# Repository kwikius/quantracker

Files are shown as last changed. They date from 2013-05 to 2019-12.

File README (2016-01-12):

DIY Antenna Tracker and OSD using STM32F4 .

Ground side tracker.
   Uses a Pololu style servo motor with encoder to give continuous Azimuth rotation
   Uses a standard RC Servo for elevation.
Airborne side 
   uses an OSD with telemetry via the video to send telemetry data to the tracker.
   or an Arduino ( basic option if you have a FrSky Telemetry RC system)

see my website http://www.zoomworks.org/fpv/quantracker/doc/index.html for more info about the project.

See the Changelog file in this directory for changes after 16/07/2013

Acknowledgments

      With Grateful Acknowledgements to the prior work, on the OSD code of:

        Sami Korhonen(Openpilot.org)
        taulabs ( taulabs.com) 
        brainFPV ( brainfpv.com)
        Thomas Oldbury (super-osd.com)
   
        Thanks to VEX Robotics for permission to use their step file of the VEX turntable

        Special Thanks to Andrew Fernie for his work on the Hardware and Software.

Dependencies

   The GNU gcc compiler. The source code is written in C++11, and requires gcc4.7 or higher
   to compile.
   available from 

         https://launchpad.net/gcc-arm-embedded
         (wget https://launchpad.net/gcc-arm-embedded/4.9/4.9-2014-q4-major/+download/gcc-arm-none-eabi-4_9-2014q4-20141203-linux.tar.bz2 -O gcc-arm)

   The STM32F4 standard peripherals library
   available from

         http://www.st.com/st-web-ui/static/active/en/st_prod_software_internet/resource/technical/software/firmware/stm32f4_dsp_stdperiph_lib.zip
         (wget http://www.st.com/st-web-ui/static/active/en/st_prod_software_internet/resource/technical/software/firmware/stm32f4_dsp_stdperiph_lib.zip -O stm32f4_dsp_stdperiph_lib.zip)

   My quan library 
   available from
         
         https://github.com/kwikius/quan-trunk
         (wget https://github.com/kwikius/quantracker/archive/master.zip -O quantracker.zip)

   FreeRTOS
   available from

         http://www.freertos.org/a00104.html
         (wget http://downloads.sourceforge.net/project/freertos/FreeRTOS/V8.2.0/FreeRTOSV8.2.0.zip -O freertos.zip)

   MAVlink
   available from
 
        https://github.com/mavlink/mavlink
        (wget https://github.com/mavlink/c_library/archive/master.zip -O mavlink.zip)
         TODO May need some file dir renaming to get the directories right for compiling

Once these are installed you will need to modify the paths in the Makefiles to suit your configuration.
See the file Sample-Dependencies.mk in the root directory for details of how to fill in dependencies

The ground tracker relies on some means on the aircraft to get the telemetry back to the tracker

The OSD can however be built as stand alone item. There are currenetly 2 customised example OSD,s in the quantracker/examples directory.
airborne option to send the data to the tracker from the aircraft.

So far there are several airborne options

  1) Use the OSD airborne module which uses the Video link direct to send telemetry.
     This is currently in development but the design is all open source and in the repo.
     I hope to have a retail version soon.

  2) using an Arduino Pro Mini microcontroller and an FrSky Rx ( simple cheap)

     a) Use an Frsky Telemetry receiver and an Ardupilot to acquire the GPS data.
      The source code for this option can be downloaded from

         https://github.com/kwikius/mavlink_to_frsky

     b) Use a GPS module attached direct to the Arduino and sending data down the FrSky telemetry link
      The source code for this option is available at
         
         https://github.com/kwikius/quantracker_air

----

   There are various other applications associated with the project. 

      See https://github.com/kwikius?tab=repositories for more details

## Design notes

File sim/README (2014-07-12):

PC simulator for my Antenna Tracker with a GUI to move the aircraft around
 and send the simulated GPS info to the Tracker.

See http://www.zoomworks.org/fpv/antenna_tracker/index.html for more about info about the Tracker.
See https://github.com/kwikius/mavlink_to_frsky for the airborne part of the project.
See https://github.com/kwikius/quantracker for sourcode for the tracker part of the project

The code is written in C++11 , so you will need gcc4.7 or above to compile and build.

Currently builds for Linux only.

Other dependencies:
 
	wxWidgets http://www.wxwidgets.org/
	my quan library:  https://github.com/kwikius/quan-trunk

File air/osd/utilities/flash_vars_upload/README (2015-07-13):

README for flash_vars.exe

This app can be used to read to :

   *  Write the flash variables to the OSD from a file
   *  Read  the flash variables to a file from the OSD. The file can then be used to
      write the Flash on other boards
   
There should be a sample file called osd_params.txt in this directory.
in the file empty lines and lines starting with '#' should be ignored

sample read invocation:
# ./flash_vars.exe -read osd_params.txt -port /dev/ttyUSB0

sample write invocation:
# ./flash_vars.exe -write osd_params.txt -port /dev/ttyUSB0

Changelog

Can now read from flash variables to a file

Fixed vector values can now contain whitespace
  e.g [ 1 ,2 , 3 ] is accepted

Fixed so that accepts return and linefeed as end of line char
Now automatically exits to start OSD when done. (Hope eventually to do it interactively
, so its wysiwyg)

Issues. 
- Check that the OSD is on and connected in flash menu mode. 
**If it isnt this app doesnt notice** So do look at the output
You can tell if its working by the text or lack of returned by the OSD.

- The array values shouldnt contain spaces else will fail,
 e.g [1,2,3] not [ 1 ,2 , 3 ] (Hope to fix this at some stage)

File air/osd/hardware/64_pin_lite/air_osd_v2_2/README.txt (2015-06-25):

The Quantracker Air OSD V2.2 files in this zip file are also available at https://github.com/kwikius/quantracker/tree/devel/air/osd/hardware/64_pin_lite/air_osd_v2_2/

*components/*
   contains "placement_bom.csv", the component placement BOM and  "component_orientation.txt", a specification of the component orientation . 
   
   	If the component orientation specification and  the resulting placement BOM is unsatisfactory, I will be happy to redo it
   	using an alternative transform for the components if you wish.
   	
      In the placement BOM, I have left the part numbers for the chip resistors and capacitors blank since you may prefer to use your own stock, however 
      I can provide some part numbers if this is more convenient. I can also provide more detailed component information if required.

*pcb/*
   contains The Gerber and Drill files.
   	The Gerber files are available in Gerber, Pdf and Postscript formats in the gerber/ subdirectory
  	   The pdf_gerbers/ and postscript_gerbers/ subdirectories contain mirrored and un-mirrored versions of the bottom layer Gerber files as pdf's and postscript format for viewing.
  	   gerbers-README.xls contains some information to help identify the layers the Gerber files represent and the suggested layup.
   
*schematic/*
   contains the schematics for the project in Pdf and Postscript formats. The kicad_project/osd.sch file can be navigated using KiCAD EESchema if preferred.

*kicad_project/*
   contains KiCad project files and some raw KiCAD output. Please be aware that some of the raw kicad output has been modified to try to fit a more standard format.

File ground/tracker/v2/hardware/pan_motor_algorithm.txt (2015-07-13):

Pan motor servo algorithm

variables
pan_motor{
 target_position;     
 target_velocity;
 desired_velocity_at_target;     
 actual_position;
 actual_velocity ;
 actual_current;
}

Unlike a position servo this one may want to be moving
Lookup target_velocity for position_error and  add desired_motor_velocity_at_target

interrupt on compare
1) calc_pwm_for next_cycle
2) start_pwm
3) end_pwm. start pan_motor_current conv
4) get pan_motor_current. calc time to start v sampling
5) start of vsampling set up DMA or irq to read velocity
6) end of vsampling dma or irq

resources

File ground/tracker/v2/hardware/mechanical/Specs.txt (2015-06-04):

-------------------------
CAD drawing of V2 tracker
-------------------------

Conventions
When horizontal and facing north, tracker looks along increasing x axis
When standing upright facing North, then Increasing Y is West
Increasing Z is up.

Axes.
The Tracker tilts around the Y axis.
The tracker pans around the Z axis.
So the intersction of the pan and tilt axes is at [0,0,0]

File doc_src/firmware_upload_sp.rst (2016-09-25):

`OSD Index`_

======================================
Uploading firmware via the Serial Port
======================================

--------
Hardware
--------

   To flash with stm32Flash you need a PC serial port and a USB TTL serial connector.
   A 6 pin Arduino Serial connector works well. It can be either a 3 volt
   or 5 volt one [1]_, but must have power out, since the programming serial port
   is electrically isolated from the rest of the board. When connected
   a red LED should light right by the connector.
   Make sure that you connect to the OSD board with the Black wire
   connected to the V-Blk pin on the 6 way connector.

   

   Alternatively you can use any usb to TTL serial connector and connect the pins appropriately.
   The OSD pins have some protection so within reason it should be possible to swap the Tx and Rx
   connections if it isnt working. Usually (but not always) TX at one end connects to RX at the other
   and vice versa

----------
Stm32flash
----------

   Whichever operating system you use, you need stm32flash. For windows,
   download and unzip `stm32flash_win.zip`_ .

   For Linux, Download Stm32flash_ and  make [sudo] make install. You may also need to add yourself to the 'dialout'
   group to allow you access to the usb serial port: ``sudo usermod -a -G dialout $USER`` ( You will need to reboot for the change to take effect)

   For a quick and dirty upload with stm3flash, get `your desired firmware`_ and
   move the stm32flash executable into the same directory as the firmware.

   Test the execution by starting a command prompt,
   navigating to the directory where the firmware is and issuing 'stm32flash' (for Linux)
   or 'stm32flash.exe'(for Windows),
   to see if it's installed. It should show a page or so of help info.

----------------------------
Find the correct serial port
----------------------------

.....
Linux
.....

   The easiest way on Linux is to remove any usb peripherals except the usb serial connector
   and type

       ``$ setserial -g /dev/ttyUSB[01234]``

   which responds with

       ``/dev/ttyUSB0, UART: unknown, Port: 0x0000, IRQ: 0, Flags: low_latency``

   when I connect my Serial USB adaptor. To be honest if
   you have no other USB serial connectors plugged connected it will usually be /dev/ttyUSB0

.......
Windows
.......

   In Windows remove any extraneous usb devices except the usb serial connector
   and open Device Manager (type Device Manager in
   the box at the bottom of the start menu and it should come up in the list).
   Look for The Ports(COM & LPT) section and there should be an item saying 'USB Serial Port' (COMx)
   where x is a number e.g (say) COM6

----------------------
Powering The OSD board
----------------------

   You will need a power supply of between 8 and 12 Volts [2]_
   to the board ( A servo connector with power and ground connected to (say) a 12 V (3S) lipo is fine)
   and ideally a switch to be able to switch it on and off, though you can just use the connector
   but a switch makes it much easier.

------------------------------------
Checking the OSD board is recognised
------------------------------------

   When using this method of uploading, it is important to follow the sequence
   exactly as described, including the connection sequence.

   *
      Make sure that *Power is Not Connected*
      ,but that it is easy to connect power without disturbing the board.
      Ideally put a switch in the power lead.
      The reason is that touching the board or jiggling the wires
      when connecting can send spurious signals as wires connect
      and disconnect and result in the bootloader on the board not
      recognising the startup sequence correctly [3]_.

   *	Connect the programming jumper on the osd board.
   *   Connect the serial connector to the board and the PC.
   *
      Verify all connectors are the correct way round.
      The connectors are not polarised, so check and check again.

   *  At a command prompt navigate to the directory with the 'xxxx.bin' binary in.
   *
      -   Linux

         +   Assuming you are on /dev/ttyUSB0  ...
         +   *Without Pressing return after yet*, type the command 'stm32flash /dev/ttyUSB0'.

      -   Windows

         +   Assuming you are on COM6  ...
         +   *Without Pressing return after yet*, type the command 'stm32flash.exe COM6'.

   *  Switch on power to the board *without joggling the wires or touching the board* .
   *  Now Press [return] !
   *
      At this point you should see a diagnostic showing that the connection is good.
      It should look something like this::

            stm32flash - http://stm32flash.googlecode.com/

            Serial Config: 57600 8E1
            Version      : 0x31
            Option 1     : 0x00
            Option 2     : 0x00
            Device ID    : 0x0413 (STM32F4xx)
            RAM          : 128KiB  (8192b reserved by bootloader)
            Flash        : 1024KiB (sector size: 4x16384)
            Option RAM   : 15b
            System RAM   : 29KiB

            Resetting device... done.

      If not:

         + Check you are on the correct serial port using the diagnostics for your system (as stated above).
         + Check you have put on the Programming jumper.
         + Check your connections and check you didnt joggle the board too much when turning on power.

   *
      If everything is ok, then, assuming you are in the directory where your firmware
      '.bin' file is, disconnect power [4]_.

-------------------------
Programming the OSD board
-------------------------

   *  Do the steps as above, but this time change the command( assuming your firmware is called 'my_osd_firmware.bin):

  		-   Linux

  			+  'stm32flash -f -v -w my_osd_firmware.bin /dev/ttyUSB0'

  		-   Windows

  			+  'stm32flash.exe -f -v -w my_osd_firmware.bin COM6'

   *
      At this point you should see the same diagnostic as before.
      Then things will appear to hang for maybe 15 seconds with no more output, so be patient::

            stm32flash -f -v -w main.bin /dev/ttyUSB0
            stm32flash - http://stm32flash.googlecode.com/

            Using Parser : Raw BINARY
            Serial Config: 57600 8E1
            Version      : 0x31
            Option 1     : 0x00
            Option 2     : 0x00
            Device ID    : 0x0413 (STM32F4xx)
            RAM          : 128KiB  (8192b reserved by bootloader)
            Flash        : 1024KiB (sector size: 4x16384)
            Option RAM   : 15b
            System RAM   : 29KiB

   *
      Eventually you should see a progress message that the firmware is being loaded.
      This process can take a while so remember not to jiggle the board meanwhile.

   *
      Finally you should see something like the following::

            Wrote and verified address 0x080271c4 (100.00%) Done.

            Resetting device... done.

   *  Congratulations! .. Your firmware  should now be loaded on the board.

   *
      Final important step before testing its working.
      *Unplug the Programming Jumper* (Its easy to forget that step!).

`OSD Index`_

.. _`your desired firmware` :
   osd/firmwares.html
.. _`stm32flash_win.zip`:
   https://github.com/kwikius/quantracker/blob/master/bin/stm32flash_win.zip?raw=true
.. _Stm32Flash: http://stm32flash.googlecode.com
.. _`OSD Index`: osd/index.html
.. _`click here for the pinout`: v1_board.html

.. [1] You only need to connect the pins in bold in the diagram.
.. [2] It should be ok to power the board from up to 25 volts. It just hasnt been verified yet.
       Use the 12V power supply inputs rather than the 3V or 5V breakouts to power the board
       , since the startup time of the psu gives a smooth wakeup from reset.
.. [3] (This is another issue with V1 board. Ideally this can be done better on V2).
.. [4] Disconnecting power executes a reset.

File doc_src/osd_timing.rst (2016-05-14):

----------
OSD Timing
----------

The OSD uses 4 timers to control the OSD [1]_. See the diagram

  

   * Line counter
        In External synch mode Listens to the csynch pulse and counts lines
        Has 4 compare channels
         - Ch1 starts the telemetry lines
         - Ch2 ends the telemtry lines
         - Ch3 starts the OSD rows
         - Ch4 ends the OSD rows
        In internal synch mode, generates the video timing
   
   * Line timer
        Starts at the beginning of telem and OSD rows.
        Has 2 channels
          - Ch1 Opens the gate for the pixel clock
          - Ch2 closes the gate for the pixe clock
            
   * pixel-clock
         Runs as a slave of the Line timer when the gate is opened

   * Idletime sync sep measurer
         This timer

. [1] It should be possible to reduce this, TODO.

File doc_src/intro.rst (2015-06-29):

`Quantracker Index`_

=============================================== 
Introducing Quantracker Antenna Tracker and OSD
===============================================

   * `The Antenna Tracker`_
         + `More on the Antenna Tracker...`_

   * `The OSD`_
         + `More on the OSD...`_

.. * _`The Antenna Tracker`

.............................
The Antenna Tracker
.............................

   Cost effective
         The price of the Tracker should be under £100 ($150). The price of the original
         was around £120 ($180). The next iteration should save over that.

   Compact and Lightweight.
      The tracker should be small, capable of fitting in a backpack neatly
      and should be quick and easy to set up at the flying site

   Simple and reliable
      The tracker should be simple to build and use and reliable in use.

   Performance
      From the outset, the tracker has been designed with performance in mind.
      The tracker can rotate continuously in Pan, unlike some servo based trackers.

   Open source hardware and software
      `The source code is available from Github`_

   Optional ground side OSD
      As time goes on and with the high bandwidth data from the video telemetry
      It should be possible to identify a point in space through the OSD so allowing
      , for example, the position of other aircraft to be displayed.

   Continuous rotation in Pan
       The tracker uses sliprings allowing continuos rotation in pan

   Various ways to send telemetry including but not limited to
         
         + Via the video feed itself ( like teletext).
         + Via one or both of the video audio channels.
         + Via an FrSky telemetry receiver.
         + A combination of any or all of the above.

.. raw:: html

   <table><tr>
   <td>
   <iframe width="420" height="315" src="https://www.youtube.com/embed/uj_cmHMo7XM" 
   frameborder="0" allowfullscreen></iframe>
   </td>
   <td>
   <iframe width="420" height="315" src="https://www.youtube.com/embed/85SXBYkTdV0" 
   frameborder="0" allowfullscreen></iframe>
   </td>
   </tr></table>

.. `The OSD`_

.......
The OSD
.......

The On Screen Display (OSD) grew out of the inital project. 
It turns out that the video signal is capable of transmitting
and receiving at a good data rate. As the design of the airborne
transmitter continued, it was decided to make the
airborne unit a full OSD, for which the ecosystem is now well underway.

   Features
      * Open source software and hardware 
         +  `The OSD V2.1 PCB is available from OSHPark`_
         +  `The OSD source code is available from Github`_

      * Compact.
      * Freestanding - can be used with or without the tracker.
      * Works with Ardupilot, Compatible with MinimOSD. 
      * supports PAL and NTSC cameras (can switch between protocols dynamically).
      * Vector graphics.
      * Hugely customisable display, using "osd_maker" App for helping to create the display.
      * Digitally isolated Serial port to help eliminate ground loops.
      * Very versatile Expansion port with I2C, SPI etc, means the OSD can be upgraded to a full FC

   Here are some videos of the OSD in action:

.. raw:: html

   <table><tr>
   <td>
   <iframe width="420" height="315" src="https://www.youtube.com/embed/cclQAswRa8s" 
   frameborder="0" allowfullscreen></iframe>
   </td>
   <td>
   <iframe width="420" height="315" src="https://www.youtube.com/embed/Czrd15weBXM" 
   frameborder="0" allowfullscreen></iframe>
   </td>
   </tr></table>

`Quantracker Index`_

.. _`The OSD V2.1 PCB is available from OSHPark`: https://oshpark.com/shared_projects/yiU4RsLa
.. _`The source code is available from Github`: https://github.com/kwikius/quantracker/tree/master
.. _`The OSD source code is available from Github`: https://github.com/kwikius/quantracker/tree/master/air/osd
.. _`Quantracker Index`: index.html
.. _`More on the Antenna Tracker...`: ../../antenna_tracker/index.html
.. _`More on the OSD...` : osd/index.html

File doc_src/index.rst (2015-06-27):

`Home`_

=================
Quantracker Index
=================

-----------------------
Antenna Tracker and OSD
-----------------------

..................
Index of sections
..................

* `Introducing the Antenna Tracker and OSD`_

  + `OSD Index`_

  + `Antenna Tracker Index`_

.. _`Introducing the Antenna Tracker and OSD`: intro.html

.. _`OSD Index`: osd/index.html
.. _`Antenna Tracker Index`: ../../antenna_tracker/index.html
.. _`Home`: ../../../index.html

`Home`_

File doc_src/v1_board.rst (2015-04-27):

Index_

--------------------------------
The Quantracker Air OSD V1 board
--------------------------------

The V1 board is not recommended to use except as a test board. 
We would recommended the V2.1 at the moment.
The V1 board had major issues with jamming GPS. 
Passing a frequency scanner over it there was found to be a large spike
at 1575 MHz which is the GPS frequency,
therefore the V1 board is not considered flyable.
However here, for completeness, is the serial port pinout for connecting MAVLink and uploading firmware

  

and here is the pinout of the board itself 

  

.. _Index: index.html

Index_

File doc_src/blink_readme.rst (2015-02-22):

Index_

Blink
=====

Blink is a basic test firmware for the quantracker air osd V1 pcb. 
which blinks the Red heartbeat LED at around 1 Hz to test that the mcu is up and running.
The firmware file is called blink.bin and is in the quantracker/air/osd/test_firmware/blink/ directory.

See the FirmwareUpload_ section for details of how to upload the blink firmware the board.

Index_

.. _FirmwareUpload: ../../../../firmware_upload.html

.. _Index: ../../../../index.html

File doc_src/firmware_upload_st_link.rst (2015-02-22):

Index_

======================================
Uploading firmware using ST-Link
======================================

  If you have a STM32 Discovery board, an STM32 Nucleo or a STLink programmer, then you can use ST-Link. 
  For this method you will also need to make up a programming cable. 
  Using this method you can also runtime debug the board.
  In Linux, you may need to edit your UdevRules_ so you can access the port. 
  The zip contains the relevant udev files which you can add to /etc/udev/rules.d/
 
  * Windows
      ST-Link for windows can be downloaded and installed from [???] (You can also use TexaneSTLink using MinGW). This is a GUI application, though its also useable from command line
  
  * Linux
  		TexaneSTLink_ 

STLink Hardware
---------------

  To flash with ST-Link, you need the ST-Link software,
  a PC usb port and either a STM32xx-Discovery or a STM32xx-Nucleo. 
  You will also need to make a connector.

  * Windows

   -
      Download the ST-LINK software from http://www.st.com/internet/evalboard/product/251168.jsp
      Somewhere down the pag, Find "Associated software"
      There are links to two zip files. Note that they are a Free Download.
      Download the files and unzip them.
      In each resulting directory there is an installer.
      One is for the ST-LINK utility and the other is for the STLINK USB drivers 
      which Windows needs for the USB programming cable. 
      After running both installers you should have a new icon on the desktop, 
      the STM32 ST-LINK Utility.
   -
      Before continuing, you should now download the firmware from 
   -  make the connector [TODO pic of connector]
   -  Start the ST-LINK Utility Application.
   -  
      Connect to the board using Target>Connect from the Top menu.
      (You may get a warning saying the ST-LINK firmware is outdated. You can ignore this.)
   -
      Open the firmware file using File>Open File from the Top menu ..
      In the first tab above the area showing the device memory make 
      sure that "Device Memory @ 0x8000000:" is selected

   - 
      Now program the device using "Target> Program" Or "Target> Program & Verify" 
      Its easiest to deselect the Reset after programming tickbox 
      ( Not essential but we can do a reset by hand for clarity)

   -
      Select Target> Disconnect and quit the application,
      while leaving the cable and pcb connected.

Index_

.. _Index: index.html
.. _Stm32Flash: http://stm32flash.googlecode.com
.. _TexaneSTLink: https://github.com/texane/stlink/
.. _UdevRules: https://wiki.archlinux.org/index.php/udev

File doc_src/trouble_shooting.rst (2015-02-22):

----------------------------
Testing and trouble shooting
----------------------------

* Blink_

.. _Blink: air/osd/board_test/blink/readme.html

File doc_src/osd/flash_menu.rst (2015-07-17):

`OSD Index`_

------------------------------
Quantracker Air OSD Flash Menu
------------------------------

For the `osd_example1`_ and `osd_ac`_ firmwares, you can access the flash menu as follows. [#no_con_change]_

Connect a usb serial connector to the board. 
(A 3V or 5V Arduino serial connector will work fine)

  

Start a serial port console at 9600 baud with 8 bits, no parity and 1 stop bit.
Note that power must be supplied to the port which is electrically isolated
from the rest of the OSD. You can however use any supply from 3 to 5V . The supply is 
usually present on an FTDI to USB cable. 
When power is supplied a red LED will be lit close by the port.

Next supply power to the OSD. It is easiest if you use a switch inline in the power
supply rather than fumbling with connectors
When you switch on the OSD, The Serial console should present you with something similar to:

::
  
   Press return 3 times for Flash Menu

Then after a few seconds

::

   Time is up! ... Exiting to Flight mode

However if you press return 3 times immediately ( up to 3 seconds) after startup you should be
presented with:

::

   Quantracker Air OSD 2.1
   ~~~~Flash menu mode~~~~

You are now in Flash menu mode.

The various functions are available as commands.

   * help
      Displays a list of the available commands with options

   * info
      Displays some useful info. For info about a particular variable type the name
      of the variable after the command

   * show
      Displays the current values of the variables.
      For value of a particular variable type the name
      of the variable after the command. Varaiables not yet defined are shown as '#undef#'
      In case of undefined variables default values are used in the osd.

   * set
      Set variable to value. Requires the name of the variable and a value in correct format.

   * exit
      Exit the flash menu mode and start showing the OSD.

To set the values of flash variables all at once go you can also use the app in 
      `quantracker/air/osd/utilities/flash_vars_upload/`_ . See the readme there for details.

.. _`quantracker/air/osd/utilities/flash_vars_upload/`: 
   https://github.com/kwikius/quantracker/tree/master/air/osd/utilities/flash_vars_upload
.. _`OSD Index`: index.html
.. _`osd_example1` : firmwares/osd_example1.html
.. _`osd_ac` : firmwares/osd_example1.html

.. [#no_con_change]  This has been changed from earlier versions so that there is no need to change connectors to enter 
         flash menu mode

`OSD Index`_

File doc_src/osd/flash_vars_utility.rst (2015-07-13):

--------------
Flash_vars.exe
--------------

This app can be used to read to :

*  Write the flash variables to the OSD from a file
*  Read  the flash variables to a file from the OSD. 

A file read from a board can then be used to write the Flash on other boards.
   
There should be a sample file called osd_params.txt in this directory.
in the file empty lines and lines starting with '#' should be ignored

Usage:
   Connect the OSD to the PC via usb cable, but dont switch on the OSD
   run flash_vars.exe on the PC
   You should see a message to say
   
::

   -----------------Ready to Upload-------------------------
   Switch on the OSD board and then immediately press any key

On switching on the OSD it will wait approx 3 seconds looking for the sequence to
start the flash menu so if the flash_vars is too late it will not catch it.

If all goes well however, The Flash Variables file will be uploaded or downloaded to/from the OSD.

sample read invocation:

::

   ./flash_vars.exe -read osd_params.txt -port /dev/ttyUSB0

sample write invocation:

:: 

   ./flash_vars.exe -write osd_params.txt -port /dev/ttyUSB0

Changelog

* Can now read from flash variables to a file

* Fixed vector values can now contain whitespace
  e.g [ 1 ,2 , 3 ] is accepted

* Fixed so that accepts return and linefeed as end of line char
  Now automatically exits to start OSD when done. (Hope eventually to do it interactively
  , so its wysiwyg)

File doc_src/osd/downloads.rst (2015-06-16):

----------------------
OSD firmware downloads
----------------------

Since the board is a Dev board we are currently providing  some example firmwraes that are designed to be customised.
As the OSD develops we hope to  develop some classic themes. Below are the firmwares that we have currently. 

........
Example1 
........

Download from Github `firmware_example1.bin`_

This OSD firmware is designed as a minimal but useful display for use with fixed wing aircraft.

The display widgets consist of
 - a compass with integral home arrow, 
 - an artificial horizon 
 - battery voltage
 
 When the OSD display starts up and while it is waiting for a GPS lock, it displays the number of satellites and the gps status.
 
 Once a valid satellite fix is obtained, the OSD assumes it is at the home position and the Display stops showing satelliete status 
 and shows the altitude and distance from home. 

.. _`firmware_example1.bin`: https://github.com/kwikius/quantracker/blob/master/examples/osd_example1/board/main.bin

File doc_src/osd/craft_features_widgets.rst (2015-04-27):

`OSD Index`_

=========================================
craft, features and widgets.
=========================================

This section deals with my ramblings on how to categorise the things you might put on the OSD. 
The current solution is to split the OSD into ones own personal project,
however there should be eventually be a library or libraries of common stuff. 

   Craft
         Could be one of:

            + aircraft
            + watercraft
            + land vehicle
            + amphibious vehicle
            + submarine
            + etc

   Features
         Variables representing fine grained aspects of the crafts behaviour/properties/state.
         Some examples of Features of a craft. A craft may or may not have 
         a particular feature [#craft_feature]_ .

            + current time
            + current latitude
            + current longtitude
            + current altitude 
            + current pitch
            + current yaw
            + current roll
            + batteries
               - so ... Number of batteries, name per battery, capacity per battery, voltage etc?

   Widgets
         Widgets are designed based on the features they require to work [#widget_robust]_ .

            * MyCompassWidget    - requires feature current yaw 
            * MyHomeArrowWidget - requires features current latitude,current Longitude
            * MyAltitudeWidget   - requires feature Altitude ( yes really :) )
            * MyArtificialHorizonWidget - requires current pitch and current roll.

   global-feature-list
         A global list of features available, with comprehensive definitions
 
   user-feature-list 
         The features of the users craft, selected from the global list of
         features.

   available-widget-list
         A set of widgets that are available for use.
         May comprise Widgets that have been accumulated from various sources
         or created by the user or both.

   user-widget-list 
         The available-widget-list is filtered by the user-feature-list to select
         only those that use features on the user-feature-list [#filter_override]_ :

   user-firmware
         The user firmware is generated from the user-widget-list. 

`OSD Index`_

.. _Features: http://www.wikipedia.org/wiki/Feature_(machine_learning)
.. _`OSD Index`: index.html

.. [#craft_feature]  A craft with a GPS can be assumed to have latitude, longtitude, altitude etc.
.. [#widget_robust]  Widgets must be designed to be able to cope with failed requests for data.
.. [#filter_override]  It should be possible to override the filter, so a user can test some feature.

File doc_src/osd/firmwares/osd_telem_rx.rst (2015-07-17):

`OSD Index`_

---------------------
osd_telem_rx firmware
---------------------

osd_telem_rx:
   This OSD firmware is designed to demonstrate the use of the video signal to transmit data.
   You will need 2 boards. The second board should run the `osd_telem_tx firmware`_. For testing
   you can connect the transmitter OSD board video out to the receiver OSD board video in.
   The display simply shows a timer. You can customise what is shown on the osd
   See the on_telemetry_received() function defined in 
   `quantracker/examples/osd_telem_rx/rx_telemetry.cpp`_ for details.
   There is `more technical info about the telemetry here`_

   `Download osd_telem_rx firmware`_

.. _`Download osd_telem_rx firmware`: 
   https://github.com/kwikius/quantracker/blob/master/examples/osd_telem_rx/bin/main.bin?raw=true
.. _`OSD Index`: ../index.html
.. _`osd_telem_tx firmware`: osd_telem_tx.html
.. _`more technical info about the telemetry here`: ../software_devel/tech/telemetry.html
.. _`quantracker/examples/osd_telem_rx/rx_telemetry.cpp`:
   https://github.com/kwikius/quantracker/blob/master/examples/osd_telem_rx/rx_telemetry.cpp

`OSD Index`_

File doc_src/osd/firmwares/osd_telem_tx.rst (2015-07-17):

`OSD Index`_

---------------------
osd_telem_tx firmware
---------------------

osd_telem_tx:
   This OSD firmware is designed to demonstrate the use of the video signal to transmit data.
   You will need 2 OSD boards. The second OSD board should run the `osd_telem_rx firmware`_ . For testing
   you can connect the transmitter board video out to the receiver board video in.
   The display simply shows a timer. 

   You can customise what is sent. 
   See the ``on_telemetry_transmitted()`` function defined in 
   `quantracker/examples/osd_telem_tx/tx_telemetry.cpp`_ for details.
   `More technical info about the telemetry here`_

   `Download osd_telem_tx firmware`_

.. _`Download osd_telem_tx firmware`: 
   https://github.com/kwikius/quantracker/blob/master/examples/osd_telem_tx/bin/main.bin?raw=true
.. _`OSD Index`: ../index.html
.. _`osd_telem_rx firmware`: osd_telem_rx.html
.. _`More technical info about the telemetry here`: ../software_devel/tech/telemetry.html
.. _`quantracker/examples/osd_telem_tx/tx_telemetry.cpp`:
   https://github.com/kwikius/quantracker/blob/master/examples/osd_telem_tx/tx_telemetry.cpp

`OSD Index`_

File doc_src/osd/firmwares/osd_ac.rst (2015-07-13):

`OSD Index`_

---------------
osd_ac firmware
---------------

   This firmware provides:

   * 4 configurable pages switchable from an RC channel
   * Many Mavlink variables that can be switched in or out per page

   `Download osd_ac firmware`_

.. raw:: html

   <iframe width="420" height="315" src="https://www.youtube.com/embed/Czrd15weBXM" 
   frameborder="0" allowfullscreen></iframe>

.. _`Download osd_ac firmware`: https://github.com/kwikius/quantracker/blob/master/examples/osd_ac/board/bin/main.bin?raw=true
.. _`OSD Index`: ../index.html

`OSD Index`_

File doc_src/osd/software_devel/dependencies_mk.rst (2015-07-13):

`OSD Index`_

------------------------
The Dependencies.mk file
------------------------

Dependencies.mk is a makefile in the quantracker root directory
whose sole purpose is to let the quantracker makefiles 
know where to find the quantracker `dependent libraries`_ ( in other words the software 
libraries that quantracker depends on to build) see `toolchain.html`_ for details
about where to get these libraries. [#installer]_ 
You can also save the template root directory file "Sample-Dependencies.mk" 
as Dependencies.mk and edit the contents.

The format to define a makefile-variable is simply

VARIABLE = expression

(`See here more info on GNU Make`_ )

The following variables need to be defined. [#trailing]_ 

TOOLCHAIN_PREFIX 
   The top-level directory to the arm-gcc compiler toolchain. e.g if your toolchain is in
   /home/kat/armgccv1 it would  be defined as TOOLCHAIN_PREFIX= /home/kat/armgccv1/

TOOLCHAIN_GCC_VERSION 
  The version of arm-gcc. The gcc version must be equal to or greater than 4.7, as the quantracker library
  makes much use of C++11 features. You can find your arm-gcc version by
  navigating at the command line to the top-level directory of the arm-gcc toolchain. 
  From there go to the bin subdirectory and invoke  './arm-none-eabi-gcc --version'
  The output should be something like :
   
  :: 

     arm-none-eabi-gcc (GNU Tools for ARM Embedded Processors) 4.9.3 20141119 (release) [ARM/embedded-4_9-branch revision 218278]
     Copyright (C) 2014 Free Software Foundation, Inc.
     This is free software; see the source for copying conditions.  There is NO
     warranty; not even for MERCHANTABILITY or FITNESS FOR A PARTICULAR PURPOSE.

  In the above case the version is 4.9.3

STM32_STD_PERIPH_LIB_DIR 
   The path to the STM32 std peripherals library

FREE_RTOS_DIR
   The path to the FreeRTOS library

QUAN_INCLUDE_PATH
   The path to the quan library (github/quan-trunk)

MAVLINK_INCLUDE_PATH 
   The path to the mavlink library

STM32FLASH
   The path to invoke the stm32flash executable

.. _`See here more info on GNU Make`: http://www.gnu.org/software/make/manual/make.html
.. _`OSD Index`: ../index.html
.. _`dependent libraries`: toolchain.html
.. _`toolchain.html`: toolchain.html
.. _`installer script`: https://github.com/kwikius/quantracker/blob/master/bin/quantracker_deps_installer.py

.. [#trailing] N.B. Dont forget the trailing '/' on any directories

.. [#installer] If you use the `installer script`_ it will create and install a Dependencies.mk file automatically

`OSD Index`_

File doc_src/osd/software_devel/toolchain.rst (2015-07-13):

`OSD index`_

------------------------------------------------------
Getting the Quantracker OSD toolchain and Dependencies
------------------------------------------------------

TODO: Windows version

To build Quantracker OSD firmwares, you need The `quantracker dependencies`_ below. 

---------------------------------
Getting dependencies the easy way
---------------------------------

The easy way is to use the `Quantracker_dependencies installer`_. Its currently Linux only,
but I hope to have it working on Windows soon. To use:

   * Download the script. 
   * Create an empty download directory
   * Call the script with Python_. 

You can add an optional directory to put the dependencies on the command line,
else you will be prompted for a download directory.

The download script attempts to retrieve and unpacks the dependencies and install everything
including the quantracker library itself, in your chosen install directory. The script also
attempts to write the `Dependencies.mk`_ file, which is used by the quantracker library
to find paths to dependent libraries, without having to create environment variables etc. .

The script is young so may have issues. I am hoping there will be a dedicated discussion forum soon to
answer questions about the project interactively.
 
------------
The hard way
------------

If you already have a dependency installed, no problem
since we can direct the toolchain to use it ( see the last part of this section). 
If you dont, then it is up to you where you wish to install the dependencies.
For myself, I use an external 'lib' directory in my home directory 
and install everying in there for simplicity. This avoids cluttering the system directories, but
you may use multiple directories (for example if you already have some of the dependencies).

.......................
Installing the hard way
.......................

Once the libraries have been downloaded, follow the per-dependency installation instructions  
below to install them. You may wish to combine the next step here..

Next, in order to get the compiler to find everything , Enter the quantracker directory
,open the `Sample-Dependencies.mk`_ in a text editor and save it as a file 
named 'Dependencies.mk' in the same root quantracker directory. Edit the defines therein 
to point to the downloaded dependency libraries. See `Dependencies.mk`_ for more details

That completes the basic installation. 

-------------------------------
Testing everything is installed
-------------------------------

Note: In the following I assume that you have renamed the quantracker download root directory to
'quantracker'. if not just substitute your own version of the name.

To test the installation you can build the osd libraries inside the quantracker distro.

At the command line, navigate into the root quantracker directory and type 'make osd_libs'. If all goes well,
building the osd driver libraries will take a few minutes.
If you see error messages, they will probably be because some header can't be found. 
In that case check that you have entered your paths to the dependencies correctly in your Dependencies.mk. 
(in most cases The relevant dependency not found  may be clear from the  error messages.)

If the osd libraries have been built correctly they should now appear in the quantracker/lib/osd/ subdirectory
as follows:

- flash_variables.a  
- quantracker_air_graphics_api.a  
- quantracker_air_osd.a  
- quantracker_air_osd_rx.a  
- quantracker_air_osd_tx.a  

--------------------------
Building a sample firmware
--------------------------

 At a command line in the quantracker root directory invoke 'make' with no arguments
 This should bring up some text detailing the various firmwares that can be built. 
 The text also details uploading firmwares from the root directory.
 See `the firmwares section`_ for currently available firmwares.
 
.. _`quantracker dependencies`:

----------------------------
The Quantracker Dependencies
----------------------------

The versions here will probably have been superceded now.
The latest stable versions are to be preferred, but to get started the ones linked here should work fine.

`arm-gcc`_
   arm-gcc compiler.
      To install, simply unzip to its target directory.

`mavlink`_
   mavlink library. 
      To install, unzip to its target directory and then
      Rename the root directory that appears('c_library-master') to 'mavlink'
   
`quan`_
   The quan library.
      To install , simply unzip to its target directory

`freertos`_
   freeRTOS real-time operating system.
      To install, simply unzip to its target directory 

`quantracker`_
   The quantracker source code and utilities.
      To install simply unzip to its target directory

`stm32`_
   stm32f4 std peripherals library.

`stm32flash`_
   utility for programming the OSD via the serial port. Download and make for linux. For Windows a prebuilt version
   is included in the quantracker/bin/ directory
   
.. _`Dependencies.mk`: dependencies_mk.html
.. _`Quantracker_dependencies installer`: https://github.com/kwikius/quantracker/blob/master/bin/quantracker_deps_installer.py
.. _`arm-gcc`:  https://launchpad.net/gcc-arm-embedded/4.9/4.9-2014-q4-major/+download/gcc-arm-none-eabi-4_9-2014q4-20141203-linux.tar.bz2
.. _`mavlink`: https://github.com/mavlink/c_library/archive/master.zip
.. _`quan`: https://github.com/kwikius/quan-trunk/archive/master.zip
.. _`freertos`: http://downloads.sourceforge.net/project/freertos/FreeRTOS/V8.2.0/FreeRTOSV8.2.0.zip
.. _`quantracker`: https://github.com/kwikius/quantracker/archive/master.zip
.. _`stm32`: http://www.st.com/st-web-ui/static/active/en/st_prod_software_internet/resource/technical/software/firmware/stm32f4_dsp_stdperiph_lib.zip
.. _`OSD index`: ../index.html
.. _`Sample-Dependencies.mk`: https://github.com/kwikius/quantracker/blob/master/Sample-Dependencies.mk
.. _`stm32flash`:  http://sourceforge.net/projects/stm32flash/files/stm32flash-0.4.tar.gz
.. _`the firmwares section`: ../firmwares.html
.. _Python: https://www.python.org

----------------------------

`OSD index`_

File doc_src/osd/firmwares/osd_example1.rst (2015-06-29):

`OSD Index`_

---------------------
osd_example1 firmware
---------------------

osd_example1:
   This OSD firmware is designed as a minimal but useful display for use with fixed wing aircraft
   The firmware  provides:

   * home distance
   * altitude
   * compass
   * home arrow
   * battery level

   `Download osd_example1 firmware`_

.. raw:: html

   <iframe width="420" height="315" src="https://www.youtube.com/embed/cclQAswRa8s" 
   frameborder="0" allowfullscreen></iframe>

.. _`Download osd_example1 firmware`: https://github.com/kwikius/quantracker/blob/master/examples/osd_example1/board/bin/main.bin?raw=true
.. _`OSD Index`: ../index.html

`OSD Index`_

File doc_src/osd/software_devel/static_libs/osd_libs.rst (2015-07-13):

-----------
Static libraries
-----------

quantracker_air_system.a
   system files for Freertos, startup etc
		
quantracker_air_osd.a  
   OSD driver without telemetry

quantracker_air_osd_tx.a
   OSD driver with transmit telemetry

quantracker_air_osd_rx.a  
   OSD driver with receive telemetry

flash_variables.a 
   Flash routines
 
quantracker_air_graphics_api.a
   graphics api routines

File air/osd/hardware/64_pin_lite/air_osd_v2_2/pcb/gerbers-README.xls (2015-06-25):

Layer Tag Name | Layer Type | Gerber File name | Visual identification | Relative position in the PCB | KiCad PCBNew Layer name (N.B inner layer name numbering is reversed with repect to Gerber files naming)
CopperLayer1-Top | copper | osd_v2_2_CopperLayer1-Top.GTL | Has the STM32F4 MCU TQFP64 footprint ,as well as other component footprints including various IC's | Top Component layer | Front
CopperLayer2-Highest_Inner | copper | osd_v2_2_CopperLayer2-Highest_Inner.G2L | Has 2 copper pours which cover the board almost entirely. The Pads at the board edge are surrounded by fill. No component footprints | Next down from “CopperLayer1-Top” | Inner3
CopperLayer3-Lowest_Inner | copper | osd_v2_2_CopperLayer3-Lowest_Inner.G3L | Has 2 copper pours that dont go right to the board edge. Pads are separately visible at the edge of the board. No component footprints | Next down from “CopperLayer2-Highest_Inner” | Inner2
CopperLayer4-Bottom | copper | osd_v2_2_CopperLayer4-Bottom.GBL | Has 4 large 1206 Capacitor footprints in a block as well as other small component footprints. Does not have any TQFP64 Footprints | Bottom Component layer. Next down from “CopperLayer3-Lowest_Inner” | Back
SolderMask1-Top | Solder mask | osd_v2_2_SolderMask1-Top.GTS
SolderMask2-Bottom | Solder mask | osd_v2_2_SolderMask2-Bottom.GBS
SolderPaste1-Top | Solder paste | osd_v2_2_SolderPaste1-Top.GTP
SolderPaste2-Bottom | Solder paste | osd_v2_2_SolderPaste2-Bottom.GBP
SilkScreen1-Top | Silkscreen | osd_v2_2_SilkScreen1-Top.GTO
Silkscreen2-Bottom | Silkscreen | osd_v2_2_SilkScreen2-Bottom.GBO
BoardOutline | Board outline | osd_v2_2_BoardOutline.GKO
DrillFile | Drill file | osd_v2_2_DrillFile.XLN
The suggested layup | dimensions/ material
CopperLayer1-Top | 1 oz copper
Layer1 to Layer2 substrate | 6.7 mil FR408
CopperLayer2 - HighestInner | 1/2 oz copper
Layer2 to Layer3 substrate | 47 mil FR408
CopperLayer3 | 1/2 oz copper
Layer3 to layer 4 subtrate | 6.7 mil FR408

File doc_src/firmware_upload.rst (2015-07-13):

`OSD Index`_

=========================================
Uploading firmware to the Tracker and OSD 
=========================================

There are 2 methods of uploading the Tracker and OSD firmwares

*  `Using the serial port`_  is the the recommended  method for the OSD,
   though the OSD board also breaks out the SW-DP Jtag debug pins, 
   and can be programmed/debugged via the SW-DP port, `Using ST-Link`_ , if required
  	
*  `Using ST-Link`_ is the recommended for the Tracker since it incorporates a ST-Link programmer.

.. _Using the serial port: firmware_upload_sp.html
.. _Using ST-Link: firmware_upload_st_link.html
.. _Index: index.html
.. _`OSD Index`: osd/index.html

`OSD Index`_

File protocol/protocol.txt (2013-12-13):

The 3 values that are sent are Latitude, longtitude and altitude

Latitude and longtitude are sent in an int32_t which has units of deg10e7
( one degree is 10^7 of these units)

Altitude is sent in an int32_t which has units of meters

transport protocol

For sending down the FrSky telem link
For FrSky 2 layer protocol. First the data must be unwrapped from the FrSky protocol.

The original tracker aircraft position protocol (ATAPP1) for data was as follows

It is a variable length protocol, using byte stuffing and escapes. 

The raw output stream uses one character(0x5E) as a framing character to signify the beginning of a new packet
Another character(0x5D) is used as an escape signifier. When either the framing character or the escape character c is encountered in the raw input stream then an escape character is inserted and that c is replaced by (c xor 0x60) in the output stream.

The latitude longtitude and altitude data is each sent in a separate packet.
Before byte stuffing and framing each packet consists of an array ar of 6 bytes
ar[0] is an id discriminating which value is in the packet
ar[1:4] is the value of the data
ar[5] is a 1 byte checksum 

The protocol is very reliable, however I dont really like the unpredictability of the variable length byts stuffing. 
The final packet may end up nearly twice the length of the original data.
Also a 1 byte checksum is quite weak with one error in 255 getting through

**The new protocol ATAPP2 **

In the new protocol The latitude longtitude and altitude data is each sent in a separate packet as before.
Before encoding each packet consists of an array of 7 bytes
ar[0] is an id discriminating which value is in the packet
ar[1:4] is the value of the data
ar[5:6] is a 2 byte checksum using Fletcher16 algorithm for genericity.

The raw output stream uses zero as a framing character and each packet including frame is 9 bytes long exactly.

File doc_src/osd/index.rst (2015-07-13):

`Quantracker Index`_

=====================
Quantracker OSD Index
=====================

---------------------------------
OSD Installation and Introduction
---------------------------------

* `Getting started with the OSD`_
* `Available Firmwares`_
* `Uploading the firmware to the OSD board`_
* `Accessing the Flash menu`_
* `Automated Reading/writing of Flash Variables`_

----------------
Developing
----------------

* `Hello World - minimal osd application`_
* `Acquiring the toolchain`_
* `Dependencies.mk`_
* `Technical documentation`_

.. _`Hello World - minimal osd application` : software_devel/hello_world.html
.. _`Automated Reading/writing of Flash Variables`: flash_vars_utility.html
.. _`Acquiring the toolchain`: software_devel/toolchain.html
.. _`Available Firmwares`: firmwares.html
.. _`Getting started with the OSD`: ../osd_getting_started.html
.. _`Accessing the Flash Menu`: flash_menu.html
.. _`Quantracker Index`: ../index.html
.. _`Uploading the firmware to the OSD board`: ../firmware_upload.html 
.. _`Testing and troubleshooting`: ../trouble_shooting.html
.. _`Home`: ../../../../index.html
.. _`Technical documentation` : software_devel/tech/index.html
.. _`Dependencies.mk` : software_devel/dependencies_mk.html

`Quantracker Index`_

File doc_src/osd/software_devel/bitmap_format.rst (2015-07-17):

`OSD Technical Index`_

--------------------
Bitmap source format
--------------------

.....................
Structure of a bitmap
.....................
To create a custom bitmap, derive your custom class from the basic_bitmap base class 
defined in `\<quan/uav/osd/basic_bitmap.hpp\>`_ . 

It will probably help to also look at the examples 
in `quantracker/examples/osd_example1/board/bitmaps.cpp`_.

N.B. This format will probably change at some point(probably to 2 arrays , 1 for each bit) 
so it is advisable to use the `osd_maker`_ app to
generate bitmaps and fonts rather than craetng them by hand.

The bitmap structure itself is relatively simple. 
The get_data and get_size functions implement the virtual functions
in the basic_bitmap base class.  The array is declared constexpr as a hint to the compiler 
to put it in in rom.

The format of the data array
----------------------------

The array is declared as an array of uint8_t, 
but should be seen as a linear array of 2 bit values, each representing a pixel.
The 2 bit values map to colours as follows (Also see `\<quan/uav/osd/colour.hpp\>`_ )

   * 0b00 = grey
   * 0b01 = white
   * 0b10 = black
   * 0b11 = transparent

The array is split into rows based on what the get_size function you provided returns.

...................
Joining it together
...................

To see how to join it up, look in  `quantracker/examples/osd_example1/board/bitmaps.cpp`_ , 
which has all the bitmaps for the example.

First look at the end of bitmaps.cpp where the get_bitmap(uint32_t id) function is defined.
As you can see, the function looks up the particular bitmap up in the bitmap_array defined above.
Note also that all bitmaps are declared in an anonymous namespace [1]_ .

In the example ,all the available bitmaps are defined in this file, which gets unwieldy.
If you want to put your bitmaps in different source files,
you can of course just #include them inline inside the anonymous namespace in this file, 
which gives the same effect but is easier to work with.

...............
Testing bitmaps
...............

For a quick test of your own bitmaps , have a look at the example in
`devel : quantracker/examples/cmd_line_bmp_output/main.cpp`_ , which outputs an ascii-art bitmap on the commandline.
(Build it with make in that directory). 
The default ouput looks like so:

::

   ~~     ~~~~~~~~
   ~  ###  ~~~  ~~
     #   ## ~ ## ~
    ##     #  ## ~
    ##      ##  ~~
    ##      ##  ~~
    ###    #  #  ~
     ###  #    # ~
   ~ ####      #  
   ~~ ####      # 
   ~~~ ####     # 
   ~~~~ ####    # 
   ~~~~ ########  
   ~~~~ ## ####  ~
   ~~~  ##      ~~
   ~~  #### ~~~~~~
      ######   ~~~
    ########## ~~~
               ~~~

.. _`\<quan/uav/osd/basic_bitmap.hpp\>`: 
   https://github.com/kwikius/quan-trunk/blob/master/quan/uav/osd/basic_bitmap.hpp
.. _`quantracker/examples/osd_example1/board/bitmaps.cpp`: 
   https://github.com/kwikius/quantracker/blob/master/examples/osd_example1/board/bitmaps.cpp
.. _`\<quan/uav/osd/colour.hpp\>` : 
   https://github.com/kwikius/quan-trunk/blob/master/quan/uav/osd/colour.hpp
.. _`devel : quantracker/examples/cmd_line_bmp_output/main.cpp`: 
   https://github.com/kwikius/quantracker/blob/master/examples/cmd_line_bmp_output/main.cpp
.. _`OSD Technical Index`: tech/index.html
.. _`osd_maker`: ../osd_maker/index.html

.. [1] Putting things in an anonymous namespace in a C++ source file is similar to one useage of static in C. 
       You can use static too, but an anonymous namespace can be neater.

`OSD Technical Index`_

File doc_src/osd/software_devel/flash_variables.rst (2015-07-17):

`OSD Technical Index`_

---------------
Flash Variables
---------------
The OSD has a mechanism for persistent storage of variables in Flash memory.
The stm32f4 mpu doesnt have EEPROM memory but it is possible to write to Flash [#flash_wear]_ .

Each flash variable must have a unique name.
and each Flash variable must have a type. Currently available types are:

   * bool
   * int8_t
   * int16_t
   * int32_t
   * uint8_t
   * uint16_t
   * uint32_t
   * float
   * three_d::vect<int32_t>
   * three_d::vect<float>
   * char[10] [#TBA]_
   * char[20] [#TBA]_
   * char[30] [#TBA]_
   * char[40] [#TBA]_

The system is designed so you can write a custom set of flash variables for your own display. 
It is suggested that you use `quantracker/examples/osd_example1/common/flash.cpp`_ as a template.
The flash symbol table named flash_variable_symtab is defined around 2/3 way down the page.
The EE_SYMTAB_ENTRY macro can be used to ease defining entries.
The symtab_entry_t structure is defined in the quan::stm32::flash namespace `\<quan/stm32/flash.hpp\>`_

::

   struct symtab_entry_t {
      const char* const name;  // user name of the symbol
      uint32_t const type_tag;  // id representing the type of the variable
      bool (*pfn_validity_check)(void*); //range check function 
      const char * const info; // some help about the flash variable
      bool readonly;  // if the value is readonly ( not writable from user flash menu)
   };

Fields:
   * name
         The name of each variable should be unique within 
         the flash variable namespace.

   * type_tag 
         To find the type tag, it is suggested to use the EE_SYMTAB_ENTRY macro. 
         In order for this to work a structure has been defined around 1/3 down the page in `flash.cpp`_ 
         called flash_variable_type, whose sole purpose is to provide a typedef of the flash variable 
         in form of its name for the EE_SYMTAB_ENTRY.

   * pfn_validity_check
         The range check function, pfn_validity_check, takes a void \* argument as input. The void \* should
         be converted to a pointer to the type of the variable to be checked. It isnt const so you can
         modify the original. All the usual caveats when using void * apply!
         In `flash.cpp`_ there is a function called nop_check, which does nothing and 
         can be used if you dont need range checking.

   * info
         Holds a small bit of helpful info about the variable which the user can read via the flash-menu.

   * readonly
         Set this true so that the variable can be read but not modified from the flash-menu. You can
         of course modify it in code, using the set_flash_value(name, value) functions 
         defined in `\<quan/stm32/flash/flash_convert.hpp\>`_  [#stw]_

-------------------------------------
viewing and modifying flash variables
-------------------------------------

      The flash variables can be viewed and modified by the flash menu or programmatically in code.
      Not that modifying flash while the OSD is running (ie once the scheduler has started)
      is a "stop the world" operation [#stw]_
      Though the actual write of a location is quite quick around 20 usec,
      it may very occasionally require erasing a page and
      copying all variables to another page which may take considerably longer. 
      I hope to try to implement it at some point but it may make the screen flicker.
      I hope also to provide facilities to access external memories as well.

      See also `accessing flash variables via the flash menu`_
      
.. _`accessing flash variables via the flash menu`: ../flash_menu.html
.. _`OSD Technical Index`: tech/index.html
.. _`\<quan/stm32/flash.hpp\>`: https://github.com/kwikius/quan-trunk/blob/master/quan/stm32/flash.hpp
.. _`\<quan/stm32/flash/flash_convert.hpp\>`: https://github.com/kwikius/quan-trunk/blob/master/quan/stm32/flash/flash_convert.hpp
.. _`quantracker/examples/osd_example1/common/flash.cpp`: https://github.com/kwikius/quantracker/blob/master/examples/osd_example1/common/flash.cpp
.. _`flash.cpp`: https://github.com/kwikius/quantracker/blob/master/examples/osd_example1/common/flash.cpp
.. [#flash_wear] Excessive Wear on the flash is prevented as follows.
                 2 flash pages are used.
                 When the flash variable value is changed, a new version of the variable is
                 appended to flash page (if there is room) until the whole page is used up.
                 To read the algorithm cycles through to find the latests version of the variable written.
                 Once the page is filled the flash variables are all copied to the other page 
                 and the cycle repeats.
.. [#TBA] null terminatd strings To be added.
.. [#stw] If the scheduler is running you need to suspend the OSD . TODO how to suspend the OSD

`OSD Technical Index`_

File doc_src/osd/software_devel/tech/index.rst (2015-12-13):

-------------------------------------------
QuantrackerAir OSD Software Technical index
-------------------------------------------

`OSD Index`_

* `Source code organisation`_
* `quan::osd::uav drawing API`_
* `Bitmap source format`_
* `Flash Variables`_
* `Telemetry`_
* `Telemetry_protocols`_
* `Quan`_
* `osd_maker`_

`OSD Index`_

.. .............Links............

.. _`quan::osd::uav drawing API`: quan/drawing_api.html
.. _`Bitmap source format`: ../bitmap_format.html
.. _`Telemetry`: telemetry.html
.. _`OSD Index` : ../../index.html
.. _`Quan` : quan/index.html
.. _`osd_maker`: ../../osd_maker/index.html
.. _`Flash Variables`: ../flash_variables.html
.. _`Source code organisation`: ../source_code_organisation.html
.. _`Telemetry_protocols` : ../../../../../antenna_tracker/telemetry/protocol.html

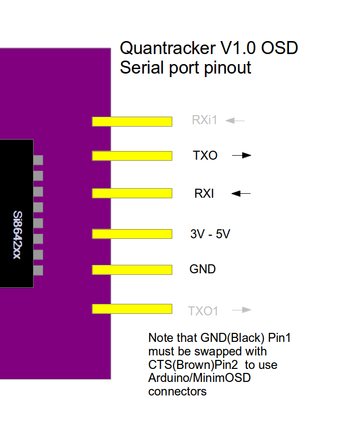
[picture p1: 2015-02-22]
doc/V1_mavlink_sp_pinout.png

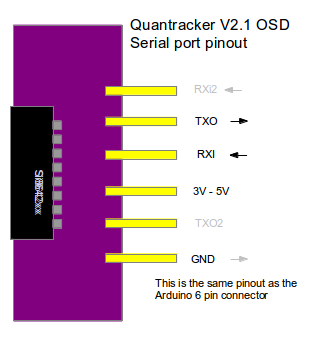
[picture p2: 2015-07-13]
doc/V2_1_mavlink_sp_pinout.png

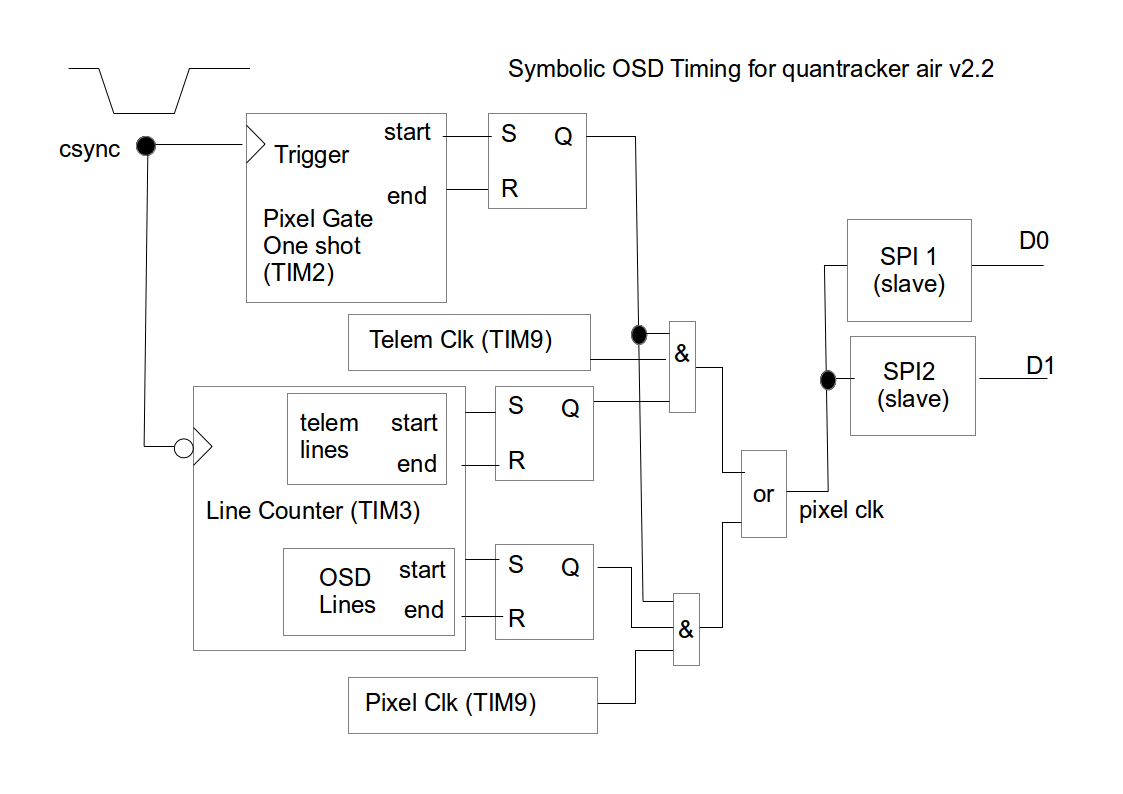
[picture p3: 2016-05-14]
doc/osd_symbolic_timing_schematic.png

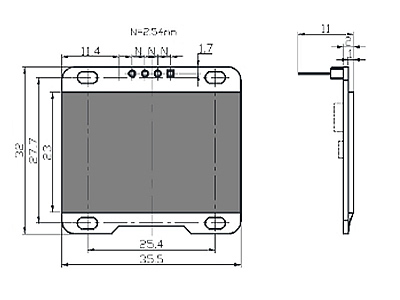
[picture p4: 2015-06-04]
ground/tracker/v2/hardware/mechanical/oled_dims.jpg

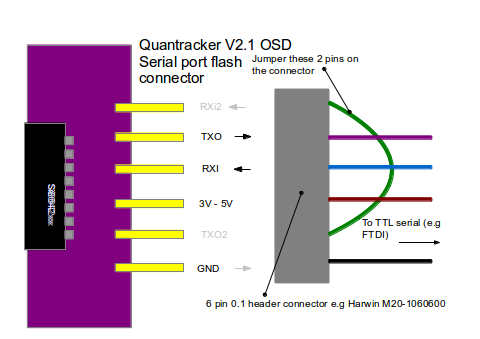
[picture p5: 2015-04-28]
doc/osd/V2_1_flash_connector.png

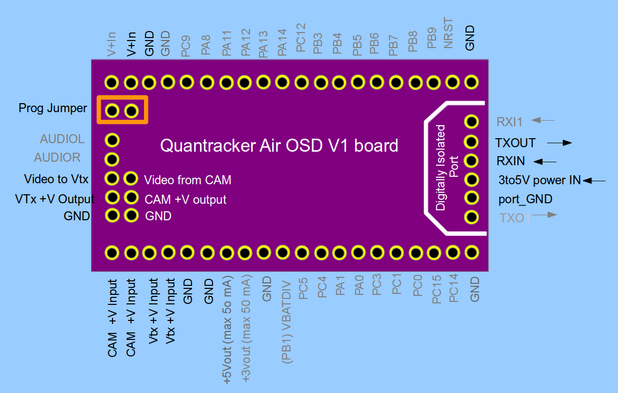
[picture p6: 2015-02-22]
doc/V1_osd_board.png

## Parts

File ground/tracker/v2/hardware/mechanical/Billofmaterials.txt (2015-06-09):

cctv power socket is a 5.5 mm x 2.1 mm socket
Multicomp Part MJ-14SR 
www.farnell.com/datasheets/1662463.pdf

4 pole jack socket
Pro-signal Part MJ-064H 
www.soselectronic.com/a_info/resource/f/mj064h.pdf

Tilt servo
HD-1501MG www.hobbyking.co.uk/hobbyking/store/__9617__Turnigy_Metal_Gear_Servo_60g_15_5kg_16sec.html

Pan motor ebay
16 mm 250 400 rpm 12 v

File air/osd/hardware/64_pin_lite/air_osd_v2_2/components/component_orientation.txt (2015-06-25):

Quantracker Air OSD V2.2 Component orientation for Pick and Place.

*Units*
  - The units of position in the Placement File are inches
  - The units of rotation are degrees

*Rotations for top and bottom layer components.*
	- A positive rotation of a component is assumed to be counterclockwise when looking down onto the top surface of the PCB, whether the component is on the Top or Bottom layer.

*Component Origin for measurements*
   - All components in this PCB are basically symmetrical and rectangular. The component origin is measured around the mean centre position of their nearest enclosing rectangle

*Component X Y Positions*
   - All components X and Y positions are measured looking down onto the top surface of the PCB, irrespective of whether the component is on the Top or Bottom layer.
   - X increases to the right and Y increases down.
   - The Fiducials FID1 (Front) and FID4 (Back) are placed at X = 0 , Y = 0
   
*Component Zero Rotations Orientation*
	The Component Zero rotations Orientation in ~./components/placement_bom.csv ( for components on the Top layer) have been calculated to conform
	functionally to IPC-7351 Feb 2005 Section 16. Bottom layer components orientations are as if a component on the Top was rotated 180 degrees around the X axis

	*Top Layer Components*

		*All SMD 2 terminal non-polarised Capacitors, Resistors and Inductors* 
	   	- Both pins have equal Y position.

      *All Diode and LED Footprints*
	    	- Both pins have equal Y position.
       	- Cathode Pin(terminal 1 in schematic) is on the left.
   
		*All IC's*
			- Pin 1 on upper left.
 
 	*Bottom Layer Components*
 
 		*All SMD non-polarised Capacitors, Resistors and Inductors* 
			- Both pins have equal Y position.
 
 		*All diode and LED footprints*
   		- Both pins have equal Y position.
   		- Cathode Pin is on the left.
 
 		*All IC's* 
  			- Pin 1 on Lower Left.

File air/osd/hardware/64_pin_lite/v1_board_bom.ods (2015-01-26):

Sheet: Sheet1
value | essential? | Qty |  | PCB id | comments | part | purchase oc | price ea | (qty regd for price) | sub total
0R | 0 | 2 | Just use wire | R24, R25 | Optional wire Links for isolated port |  | --- | 0 |  | 0
0u1 | 1 | 11 | 0603 10V | C1, C2, C4, C5, C7, C8, C10, C20, C21, C32, C33, C34, C35, C36 | 3V3 decouple caps | CL10B104KB8SFNC | Digikey 1276-1936-1-ND | 0.0089 | 100 | 0.0979
0u1 | 1 | 8 | 0603 15V | C22, C23, C26 ,C28, C29 | 5V decouple caps | “ | “ | 0.0089 | - | 0.0712
0u1 | 1 | 1 | 603 50V | C18 | Decouple cap output of switcher | “ | “ | 0.0089 | - | 0.0089
0u1 | 1 | 2 | 603 50V | C12, C40 | Vin + cap | “ | “ | 0.0089 | - | 0.0178
0u15 | 1 | 1 | 603 50V | C15 | switcher feedback res divider compensation cap | C0603C154K5RACTU | Digikey 399-9015-1-ND | 0.0516 |  | 0.0516
10uF | 0 | 1 | 0603 10V | C39 | battery voltage res divider smoothing cap | GRM188R61A106ME69D | Digikey 490-10475-1-ND | 0.101 | 10 | 0.101
100R | 1 | 9 | 603 | R4, R5, R6, R17, R19,R26, R27, R28, R29 |  | MCT06030C1000FP500 | Digikey MCT0603-100-CFCT-ND | 0.036 | 50 | 0.324
10K | 1 | 2 | 603 | R1,R7 |  |  |  | 0.0106 |  | 0.0212
10uF | 1 | 1 | 0805 10V | C19 | 3.3V linear reg decouple cap | CL21F106ZPNNNE | Digikey 1276-3012-1-ND | 0.079 | 10 | 0.079
10uF | 1 | 3 | 1206 50V | C16, C17 | 5V output side of switch reg caps each side of PI LC filter | UMK316BBJ106ML-T | Digikey 587-3248-1-ND | 0.45 |  | 1.35
15nF | 1 | 1 | 603 50V | C14 | switcher mos gate charge cap | CL10B153KB8NNNC | Digikey 1276-1277-1-ND | 0.018 | 10 | 0.018
1K | 1 | 3 | 603 | R14, R15, R16 |  |  |  | 0.0106 |  | 0.0318
20R | 1 | 2 | 603 | R20, R22 |  | ERJ-3GEYJ200V | Digikey P20.0HCT-ND | 0.0106 |  | 0.0212
2K | 1 | 1 | 603 | R18 |  | ERJ-3EKF2001V | Digikey P2.00KHCT-ND | 0.0106 | 50 | 0.0106
2u2 | 1 | 2 | 0603 10V | C3, C6 | STM32 decouple cap VCAP_1 VCAP_2 | CL10F225ZP8NNNC | Digikey 1276-1821-1-ND | 0.06 | 10 | 0.12
2.2uH | 0 | 2 | 603 | L2, L4 | switcher input and output Pi filter inductor( not essential could use a link) | MLZ1608A2R2WT (2.2 uH 0.25 ohm) | Farnell 2215629 | 0.07 |  | 0.14
33K | 0 | 1 | 603 | R12 | Comp + fdbk (only if used as RX) |  |  | 0.07 |  | 0.07
33uF | 0 | 2 | 0805 10V | C24, C25 | Audio Output Bypass (not essential) | C2012X5R1A336M125AC | Digikey 445-8238-1-ND | 0.667 |  | 1.334
40R | 1 | 1 | 603 | R21 |  | CRCW060340R2FKEA | Digikey 541-40.2HCT-ND | 0.0334 | 50 | 0.0334
250pF(240 pf) | 1 | 1 | 0603 10V 10%tol | C27 | csync lp filter cap | GRM1885C2A241JA010 | Digikey 490-1360-1-ND | 0.077 | 10 | 0.077
470R | 1 | 3 | 603 | R2, R3, R10 |  | MCT06030C4700FP500 | Digikey MCT0603-470-CFCT-ND | 0.049 | 20 | 0.147
4K1 | 1 | 1 | 603 | R8 | switcher output divider upper,Could replace with 3k9 for 5V currently gives 5.25 V output | CRCW06034K12FKEA | Digikey 541-4.12KHCT-ND | 0.0334 | 50 | 0.0334
4u7 | 1 | 1 | 1206 50V X7R X5R | C13,C41 |  | UMK316ABJ475KD-T | Digikey 587-2988-1-ND | 0.1084 | 50 | 0.1084
4u7 | 1 | 5 | 0603 10V | C9, C11, C30, C31 |  | GRM188F51A475ZE20D | Digikey 490-3302-1-ND | 0.11 |  | 0.55
1K2 | 1 | 1 | 603 | R13 | csync lp filter res | MCT06030C1201FP500 | Digikey MCT0603-1.20K-CFCT-ND | 0.049 | 20 | 0.049
680R | 1 | 1 | 603 | R9 | switcher output lower divider | MCT06030C6800FP500 | Digikey MCT0603-680-CFCT-ND | 0.049 | 20 | 0.049
74LVC1G86 | 1 | 1 | SOT23-5 | U3 | single xor to change sense of txo for frky | SN74LVC1G86DBVR | Farnell 1287521 | 0.053 |  | 0.053
75R | 1 | 2 | 603 | R11, R23 |  |  |  | 0.07 |  | 0.14
ADG704 | 1 | 1 | MSOP-10 | U12 | analog mux for osd | ADG704BRMZ | Mouser 584-ADG704BRMZ | 1.83 |  | 1.83
BD9G101G | 1 | 1 | SOT23-6 | U4 | Switcher IC for 5v output | BD9G101G | Farnell 2373587 | 0.58 |  | 0.58
Blue Led | 1 | 1 | 603 | D3 | 5v LED power indicator | APT1608QBC/D | Digikey 754-1434-1-ND | 0.1656 | 25 | 0.1656
470pF | 1 | 2 | 0603 15V | C37, C38 | isolated port rc filter caps on inputs | C0603C471KRACTU | Digikey 399-10051-1-ND | 0.08 | 50 | 0.16
CONN_1 | 0 | 5 |  | P6, P7, P8, P9, P10 | solder pads on pcb | --- |  | 0 | 0 | 0
CONN_2 | 0 | 1 |  | P1 | 0.1 pitch header pins break off strip |  |  | 0.1 |  | 0.1
CONN_20 | 0 | 2 |  | P2, P3 | “ |  |  | 0.1 |  | 0.2
CONN_3 | 0 | 1 |  | K1 | “ |  |  | 0.1 |  | 0.1
CONN_5 | 0 | 1 |  | P5 | “ |  |  | 0.1 |  | 0.1
CONN_6 | 0 | 1 |  | P4 | “ |  |  | 0.1 |  | 0.1
DAC084S085 | 1 | 1 | MSOP-10 | U11 | Colour and sync DAC | DAC084S085CIMM | Farnell 1312536 | 0.7 |  | 0.7
switcher flyback diode | 1 | 1 | SOD123 | D2 | 30 V 500 mA | MBR0530T1G | Farnell 1431036 | 0.07 |  | 0.07
input protect diode | 1 | 1 | SOD123 | D6 | 30 V 500 mA | MBR0530T1G | Farnell 1431036 | 0.07 |  | 0.07
cam v+ protect diode | 1 | 1 | SOD123 | D4 | 30 V 500 mA | MBR0530T1G | Farnell 1431036 | 0.07 |  | 0.07
Vtx V+ protect diode | 1 | 1 | SOD123 | D5 | 30 V 500 mA | MBR0530T1G | Farnell 1431036 | 0.07 |  | 0.07
22nH | 0 | 1 | 603 | L1 | MCU analog filter inductor(not essential just use a link) | CIH10T22NJNC | Digikey 1276-6310-1-ND | 0.0448 | 25 | 0.0448
FMS6141 | 1 | 1 | SC70-5 | U10 | Video driver with 4th order filter and sync clamp | FMS6141S5X | Farnell 1740322 | 0.264 |  | 0.264
LD39015MXXR | 1 | 1 | SOT23-5 | U5 | 3.3V LDO reg | LD39015M33R | Farnell 2311333 | 0.307 |  | 0.307
LM358 | 0 | 1 | MSOP-8 | U7 | Dual OpAmp for audio output ( not essential) | LM358PWR | Farnell 2323330 | 0.1345 |  | 0.1345
LPS4018-473MR | 1 | 1 |  | L3 | Switcher inductor | LPS4018-473MR (try | Farnell 2408111 | 0.56 |  | 0.56
MCP6562 |  | 1 | MSOP-8 | U8 | dual comparator push pul output | MCP6562-E/MS | Farnell 1834858 | 0.64 |  | 0.64
OPA830 |  | 0 | SOT23-5 | U13 | Video amp (try Max4390 cheaper and less feedback res reqd) | OPA830IDBVT | Farnell 1755003 | 1.52 |  | 0
MAX4390 |  | 1 | SOT23-5 | U13 | Alternative cheaper Video Amp | MAX4390 | Farnell 1550544 | 0.92 |  | 0.92
110K |  | 1 | 603 | R30 | battery voltage resistor ladder (high res) | CRCW0603110KFKEA | Digikey 541-110KHCT-ND | 0.0052 |  | 0.0052
15K |  | 1 | 603 | R31 | battery voltage resistor divider ground res |  |  | 0.07 |  | 0.07
RED LED |  | 1 | 603 | D1 | heartbeat led | APT1608EC | Digikey 754-1117-1-ND | 0.0664 |  | 0.0664
SI501 |  | 1 |  | U1 | 8 MHz osc | SI501ABA8M00000CAF | Digikey 336-2870-ND | 0.635 | 10 | 0.635
SI8642 |  | 1 | SOIC16 | U6 | digital isolator | SI8642AB-B-IS1 | Farnell 2423298 | 1.13 |  | 1.13
STM32F405RGT6 |  | 1 | LQFP64 | U2 | STM32F405RGT6 | STM32F405RGT6 | Digikey 497-11767-ND | 8.11 |  | 8.11
TLV3501 |  | 1 | SOT23-6 | U9 | Fast comparator with Hiz (only reqd if used as Rx) | TLV3501AIDBVT | Farnell 1903403 | 1.77 |  | 1.77
PCB |  | 1 |  |  | PCB from OSHPark |  | pcb | 4.2 |  | 4.2
 |  |  |  |  |  |  |  |  | total | £28.28
 |  |  |  |  |  |  |  |  | vat | £5.66
 |  |  |  |  |  |  |  |  | tot inc vat | £33.94

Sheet: Sheet2
0u1 | 603 | 50V | 50 | x | 100R | 603 | 6
0u15 | 603 | 50V | 10 | x | 20R | 603 | 3
10uF | 603 | 10V | 2 | x | 2K | 603 | 1
10uF | 1206 | 50V | 2 | x
10uF | 805 | 10V | 1 | x | 40R | 603 | 1
15nF | 603 | 50V | 1 | x | 470R | 603 | 3
2u2 | 603 | 10V | 2 | x | 4K1 | 603 | 1
33uF | 805 | 10V | 2 | x | 1k2 | 603 | 1
250pF (10%) | 603 | 10v | 1 | x | 680R | 603 | 1
4u7 | 1206 | 50V | 2 |  | 110K | 603 | 1
470pF | 603 | 15V | 3 | x
2u2 inductor | 603 |  | 2

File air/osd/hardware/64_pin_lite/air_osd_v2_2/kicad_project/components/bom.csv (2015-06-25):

ref | value | footprint | Field1 | Field2 | Field3 | Field4 | Field5 | Field6 | Field7 | Field8
C1 | 0.1uF | 0603 | M | P | Capacitor/0.1uF/10V/+-10%/X7R/0603
C2 | 0.1uF | 0603 | M | P | Capacitor/0.1uF/10V/+-10%/X7R/0603
C3 | 2.2uF | 0603 | M | P | Capacitor/2.2uF/10V/-20%+80%/Y5V/0603
C4 | 0.1uF | 0603 | M | P | Capacitor/0.1uF/10V/+-10%/X7R/0603
C5 | 0.1uF | 0603 | M | P | Capacitor/0.1uF/10V/+-10%/X7R/0603
C6 | 2.2uF | 0603 | M | P | Capacitor/2.2uF/10V/-20%+80%/Y5V/0603
C7 | 0.1uF | 0603 | M | P | Capacitor/0.1uF/10V/+-10%/X7R/0603
C8 | 0.1uF | 0603 | M | P | Capacitor/0.1uF/10V/+-10%/X7R/0603
C9 | 4.7uF | 0603 | M | P | Capacitor/4.7uF/10V/+-10%/X5R/0603
C10 | 0.1uF | 0603 | M | P | Capacitor/0.1uF/10V/+-10%/X7R/0603
C11 | 4.7uF | 0603 | M | P | Capacitor/4.7uF/10V/+-10%/X5R/0603
C12 | 0.1uF | 0603 | M | P | Capacitor/0.1uF/50V/+-10%/X7R/0603
C13 | 4.7uF | 1206 | M | P | Capacitor/4.7uF/50V/+-20%/X5R/1206
C14 | 15nF | 0603 | M | P | Capacitor/15nF/50V/+-10%/X7R/0603
C15 | 0.15uF | 0603 | M | P | Capacitor/0.15uF/35V/+-10%/X7R/0603
C16 | 10uF | 1206 | M | P | Capacitor/10uF/50V/+-10%/X5R/1206
C17 | 10uF | 1206 | M | P | Capacitor/10uF/50V/+-10%/X5R/1206
C18 | 0.1uF | 0603 | M | P | Capacitor/0.1uF/50V/+-20%/X7R/0603
C19 | 10uF | 0805 | M | P | Capacitor/10uF/10V/-20%+80%/Y5V/0805
C20 | 0.1uF | 0603 | M | P | Capacitor/0.1uF/10V/+-20%/X7R/0603
C21 | 0.1uF | 0603 | M | P | Capacitor/0.1uF/50V/+-10%/X7R/0603
C22 | 0.1uF | 0603 | M | P | Capacitor/0.1uF/50V/+-10%/X7R/0603
C23 | 0.1uF | 0603 | M | P | Capacitor/0.1uF/10V/+-10%/X7R/0603
C24 | 33uF | 0805 | M | P | Capacitor/33uF/10V/+-20%/X5R/0805
C25 | 33uF | 0805 | M | P | Capacitor/33uF/10V/+-20%/X5R/0603
C26 | 0.1uF | 0603 | M | P | Capacitor/0.1uF/10V/+-10%/X7R/0603
C27 | 240pF | 0603 | M | P | Capacitor/240pF/10V/+-5%/NPO/0603
C28 | 0.1uF | 0603 | M | P | Capacitor/0.1uF/10V/+-10%/X7R/0603
C29 | 0.1uF | 0603 | M | P | Capacitor/0.1uF/10V/+-10%/X7R/0603
C30 | 0.1uF | 0603 | M | P | Capacitor/0.1uF/10V/+-10%/X7R/0603
C31 | 4.7uF | 0603 | M | P | Capacitor/4.70.uF/10V/+-10%/X5R/0603
C32 | 0.1uF | 0603 | M | P | Capacitor/0.1uF/10V/+-10%/X7R/0603
C33 | 0.1uF | 0603 | M | P | Capacitor/0.1uF/10V/+-10%/X7R/0603
C34 | 0.1uF | 0603 | M | P | Capacitor/0.1uF/10V/+-10%/X7R/0603
C35 | 0.1uF | 0603 | M | P | Capacitor/0.1uF/10V/+-10%/X7R/0603
C36 | 0.1uF | 0603 | M | P | Capacitor/0.1uF/10V/+-10%/X7R/0603
C37 | 470pF | 0603 | M | P | Capacitor/470pF/16V/+-10%/X7R/0603
C38 | 470pF | 0603 | M | P | Capacitor/470pF/16V/+-10%/X7R/0603
C39 | 0.1uF | 0603 | M | P | Capacitor/0.1uF/10V/+-10%/X7R/0603
C40 | 0.1uF | 0603 | M | P | Capacitor/0.1uF/50V/+-10%/X7R/0603
C41 | 4.7uF | 1206 | M | P | Capacitor/4.7uF/50V/+-20%/X5R/1206
C42 | 0.1uF | 0603 | M | P | Capacitor/0.1uF/50V/+-10%/X7R/0603
C43 | 0.1uF | 0603 | M | P | Capacitor/0.1uF/10V/+-10%/X7R/0603
C44 | 4.7uF | 0603 | M | P | Capacitor/4.70.uF/10V/+-10%/X5R/0603
C45 | 0.1uF | 0603 | M | P | Capacitor/0.1uF/50V/+-10%/X7R/0603
D1 | Red_Led | 0603 | M | P | Led/Red/0603
D2 | MBR0530T1G | SOD-123 | On Semiconductor | MBR0530T1G | Diode/Schottky/30V/500mA/SOD-123
D3 | Blue_Led | 0603 | M | P | Led/Blue/0603
D4 | MBR0530T1G | SOD-123 | On Semiconductor | MBR0530T1G | Diode/Schottky/30V/500mA/SOD-123
D5 | MBR0530T1G | SOD-123 | On Semiconductor | MBR0530T1G | Diode/Schottky/30V/500mA/SOD-123
D6 | MBR0530T1G | SOD-123 | On Semiconductor | MBR0530T10G | Diode Schottky/30V/500mA/SOD-123
D7 | Red_Led | 0603 | M | P | Led/Red/0603
FID1 | FIDUCIAL | FIDUCIAL | none | none | fiducial
FID2 | FIDUCIAL | FIDUCIAL | none | none | fiducial
FID3 | FIDUCIAL | FIDUCIAL | none | none | fiducial
FID4 | FIDUCIAL | FIDUCIAL | none | none | fiducial
FID5 | FIDUCIAL | FIDUCIAL | none | none | fiducial
FID6 | FIDUCIAL | FIDUCIAL | none | none | fiducial
K1 | SIL3 | SIL3 | 0.1 in pitch header connector/3 contacts
L1 | 22nH | 0603 | Samsung | CIH10T22NJNC | Inductor/22nH/+-10%/0.4R/0603
L2 | 22nH | 0603 | Samsung | CIH10T22NJNC | Inductor/22nH/+-10%/0.4R/0603
L3 | LPS4018-473MR | LPS4018 | Coilcraft | LPS4018-473MR | Inductor/47uH
L4 | 22nH | 0603 | Samsung | CIH10T22NJNC | Inductor/22nH/+-10%/0.4R/0603
L5 | BLM18EG601SN1 | 0603 | Murata | BLM18EG601SN1 | Inductor/Bead/0603
L6 | BLM18EG601SN1 | 0603 | Murata | BLM18EG601SN1 | Inductor/Bead/0603
L7 | BLM18EG601SN1 | 0603 | Murata | BLM18EG601SN1 | Inductor/Bead/0603
P1 | SIL2 | SIL2 | 0.1 in pitch header/2 contacts
P2 | SIL20 | SIL20 | 0.1 in pitch header/20 contacts
P3 | SIL20 | SIL20 | 0.1 in pitch header/20 contacts
P4 | SIL6 | SIL6 | 0.1 in pitch header/6 contacts
P5 | SIL5 | SIL5 | 0.1 in pitch header/5 contacts
P6 | Pad | none | none | none | Test pad
P7 | Pad | none | none | none | Test Pad
P8 | Pad | none | none | none | Test Pad
P9 | Pad | none | none | none | Test Pad
P10 | Pad | none | none | none | Test Pad
P11 | SIL1 | SIL1 | 0.1 in pitch header/1 contact
P12 | Pad | none | none | none | Test Pad
R1 | 10K | 0603 | M | P | Resistor/1K/+-10%/0603
R2 | 470R | 0603 | M | P | Resistor/470R/+-10%/0603
R3 | 470R | 0603 | M | P | Resistor/470R/+-10%/0603
R4 | 100R | 0603 | M | P | Resistor/100R/+-10%/0603
R5 | 100R | 0603 | M | P | Resistor/100R/+-10%/0603
R6 | 100R | 0603 | M | P | Resistor/100R/+-10%/0603
R7 | 10K | 0603 | M | P | Resistor/10K/+-10%/0603
R8 | 4.1K | 0603 | M | P | Resistor/4.1K/+-1%/0603
R9 | 680R | 0603 | M | P | Resistor/680R/+-1%/0603
R10 | 470R | 0603 | M | P | Resistor/470R/+-10%/0603
R11 | 75R | 0603 | M | P | Resistor/75R/+-1%/0603
R12 | 33K | 0603 | M | P | Resistor/33K/+-1%/0603
R13 | 1.2K | 0603 | M | P | Resistor/1.2K/+-1%/0603
R14 | 1K | 0603 | M | P | Resistor/1K/+-1%/0603
R15 | 1K | 0603 | M | P | Resistor/1K/+-1%/0603
R16 | 1K | 0603 | M | P | Resistor/1K/+-1%/0603
R17 | 100R | 0603 | M | P | Resistor/100R/+-10%/0603
R18 | 2K | 0603 | M | P | Resistor/2K/+-1%/0603
R19 | 100R | 0603 | M | P | Resistor/100R/+-10%/0603
R20 | 20R | 0603 | M | P | Resistor/20R/+-1%/0603
R21 | 40.2R | 0603 | M | P | Resistor/40.2R/1%/0603
R22 | 20R | 0603 | M | P | Resistor/20R/+-1%/0603
R23 | 75R | 0603 | M | P | Resistor/75R/+-1%/0603
R24 | 470R | 0603 | M | P | Resistor/470R/+-10%/0603
R25 | 0R | 0603 | M | P | Resistor(Link)/0R/0603
R26 | 100R | 0603 | M | P | Resistor/100R/+-10%/0603
R27 | 100R | 0603 | M | P | Resistor/100R/+-10%/0603
R28 | 100R | 0603 | M | P | Resistor/100R/+-10%/0603
R29 | 100R | 0603 | M | P | Resistor/100R/+-10%/0603
R30 | 0R | 0603 | M | P | Resistor(Link)/0R/0603
R31 | 47K | 0603 | M | P | Resistor/47K/10%/0603
R32 | 47K | 0603 | M | P | Resistor/47K/10%/0603
U1 | SI501 | DFN2532 | Silicon Labs | SI501ABA8M00000CAF | 8 MHZ Oscillator in DFN 2.5mm x 3.2 mm
U2 | STM32F405RGT6 | LQFP64 | ST Microelectronics | STM32F405RGT6
U3 | 74LVC1G86 | SOT23-5 | Texas Instruments | SN74LVC1G86DBVR | Single_XOR_Gate/SOT23-5
U4 | BD9G101G | SOT23-6 | Rohm Semiconductor | BD9101G | Switching_Regulator_IC
U5 | LD39015MXXR | SOT23-5 | ST Microelectronics | LD39015M33R | VoltageReg/3.3V/SOT23-5
U6 | SI8642 | NSOIC-16 | Silicon Labs | SI8642AB-B-IS1 | Digital isolator/NSOIC-16
U7 | LM358DMR2G | MSOP-8 | On Semiconductor | LM358DMR2G | OpAmp/Dual/MSOP-8
U8 | MCP6562 | MSOP-8 | Microchip | MPC6562-E/MS | Comparator/Dual/MSOP-8
U9 | TLV3501 | SOT23-6 | Texas Instruments (Burr-Brown) | TLV3501AIDBVT | Comparator/Single/Hi_Z
U10 | FMS6141 | SC70-5 | Fairchild Semiconductor | FMS6141S5X | Video Amp/SyncClamp/4th Order Filter/G=2
U11 | DAC084S085 | MSOP-10 | Texas Instruments | DAC084SO85CIMM | DAC/8Bit/Quad channel/MSOP-10
U12 | ADG704 | MSOP-10 | Analog Devices | ADG704BRMZ | Analog Mux switch/4 channel/MSOP-10
U13 | OPA830 | SOT23-5 | Texas Instruments | OPA830IDBVT | VideoAmp

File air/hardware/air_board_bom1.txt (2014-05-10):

#Cmp ( order = Reference )
#far| C1         1nF         SM0805;  
           
| C2         15 pF       SM0805;             
| C3         15 pF       SM0805; 
 #far           
| C4         0.1uF       SM0805;             
| C7         0.1uF       SM0805;                      
| C10        0.1uF       SM0805;                    
| C12        0.1uF       SM0805;             
| C13        0.1uF       SM0805;             
| C14        0.1uF       SM0805;
             
| D1         Blue LED    SM0805;             
| D3         Red LED     SM0805;

| C11        1nF         SM0805; 
| C8         2nF         SM0805; (stack 2 1nF) 

| C5         10uF        SM1206;             
| C6         10uF        SM1206;

| Q1         MOSFET_N    SOT23GDS;
           
| P1         CONN_4      SIL4;             
| P2         CONN_2      SIL2;             
| P3         CONN_2      SIL2;             
| P4         CONN_1      SIL1;             
| P5         CONN_1      SIL1;             
| P6         CONN_1      SIL1;             
| P7         CONN_1      SIL1;             
| P8         CONN_1      SIL1;             
| P9         CONN_1      SIL1;             
             
| R1         1K          SM0805;             
| R2         100R        SM0805;             
| R3         100R        SM0805;             
| R4         1K          SM0805;             
| R5         470R        SM0805;             
| R6         1K          SM0805;             
| R7         470R        SM0805;             
| R8         4k7         SM0805;             
| R9         4k7         SM0805;             
| R10        100R        SM0805;             
| R11        100R        SM0805;             
| R12        4k7R        SM0805;             
| R13        4k7R        SM0805;             
| U1         LD1117      SOT223;             
| U2         STM32F051   LQFP32;             
| U3         MCP6L01     SOT23-5;             
| U4         24LC01      SOT23-5;             
| X1         8MHz        Xtal5x3.2;             
#End Cmp

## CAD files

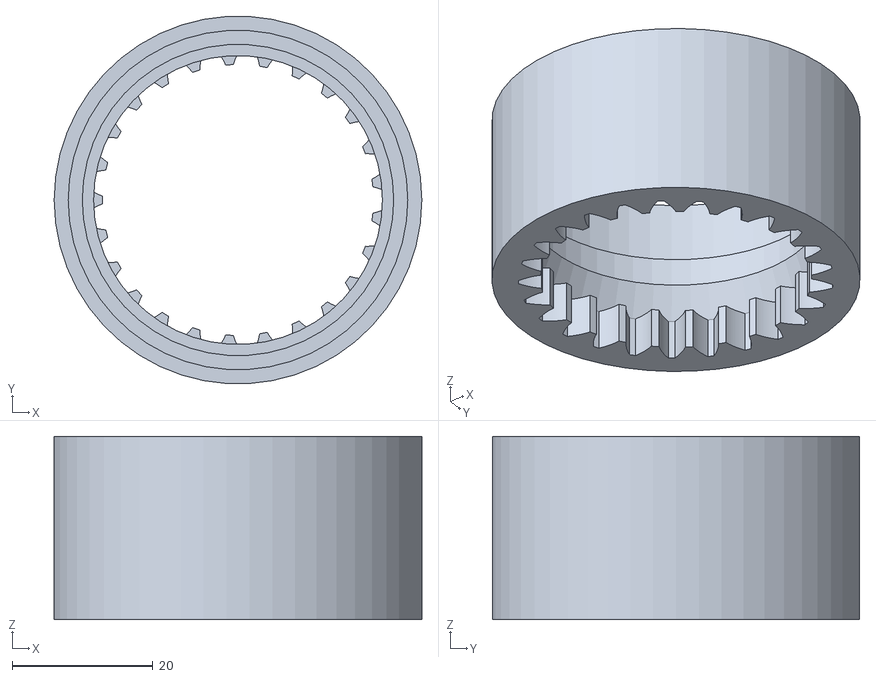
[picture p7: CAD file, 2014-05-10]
ground/tracker/scad_files/output/main_gear_outer_bearing_holder.stl
52.2 x 52.1 x 26.0

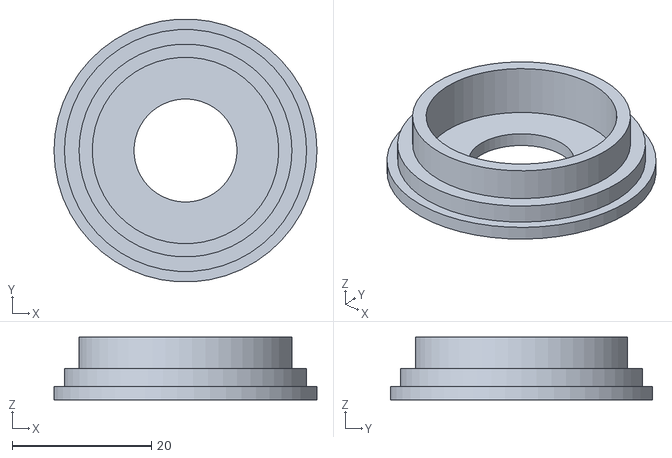
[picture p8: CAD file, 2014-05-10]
ground/tracker/scad_files/output/inner_bearing_holder.stl
37.8 x 37.7 x 9.00

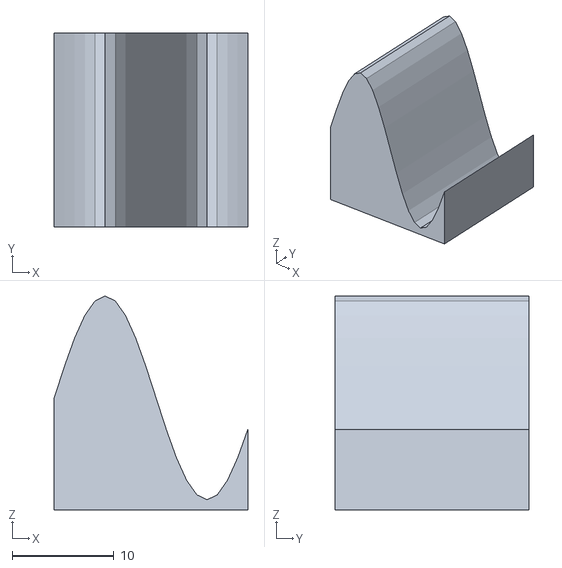
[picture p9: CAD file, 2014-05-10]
ground/tracker/scad_files/surface.stl
19.0 x 19.0 x 21.0

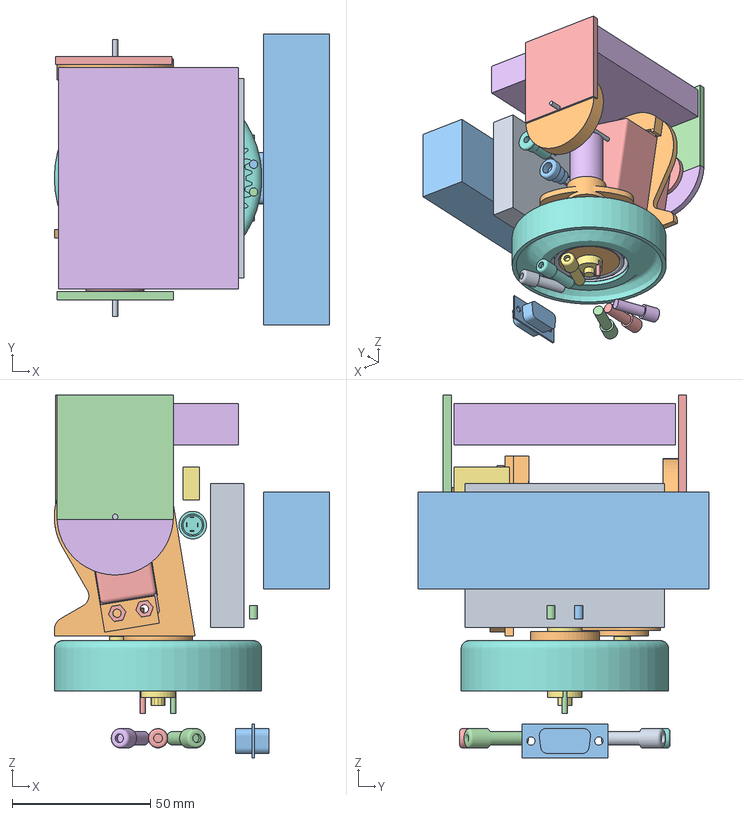
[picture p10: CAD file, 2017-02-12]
ground/tracker/v2/hardware/mechanical/slewing_ring.fcstd
99.5 x 105.0 x 131.1 mm
ballrace30x42x7
SlewingRingUpper
Screw_hole3
Screw_hole4
TiltServo
AntennaHingeRight
small_gear
SlewRingLower
tilt_axis_cylinder
PanMotorTopBracket
PowerConnector
16mmGearMotor
BalanceChargerPwrSocket
4_way_jack_socket
PcbBox
TiltServoMount
DB9_connector
RCA_socket001
RCA_socket002
RCA_socket003
RCA_socket004
RCA_socket005
RCA_socket006
AntennaHingeLeft
Battery
AntennaMount_left_leg
AntennaMount_right_leg
Vrx
slipring

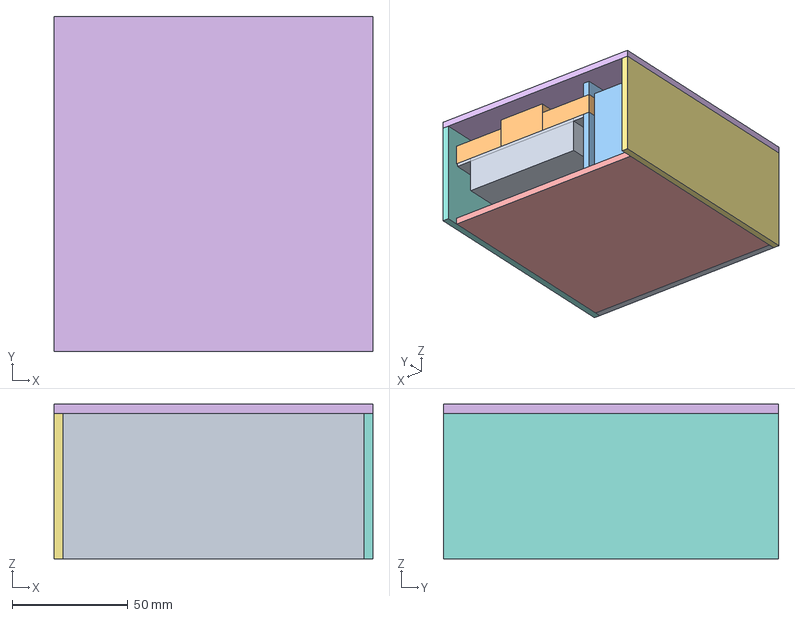
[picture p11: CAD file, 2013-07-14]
hardware/tracker_v1_base.fcstd
138.0 x 145.0 x 67.0 mm
video_distrib_amp
serial_port
Battery
sliprings
base
top
right_side
left_side
back
video_amp_support
video_amp_vert_support

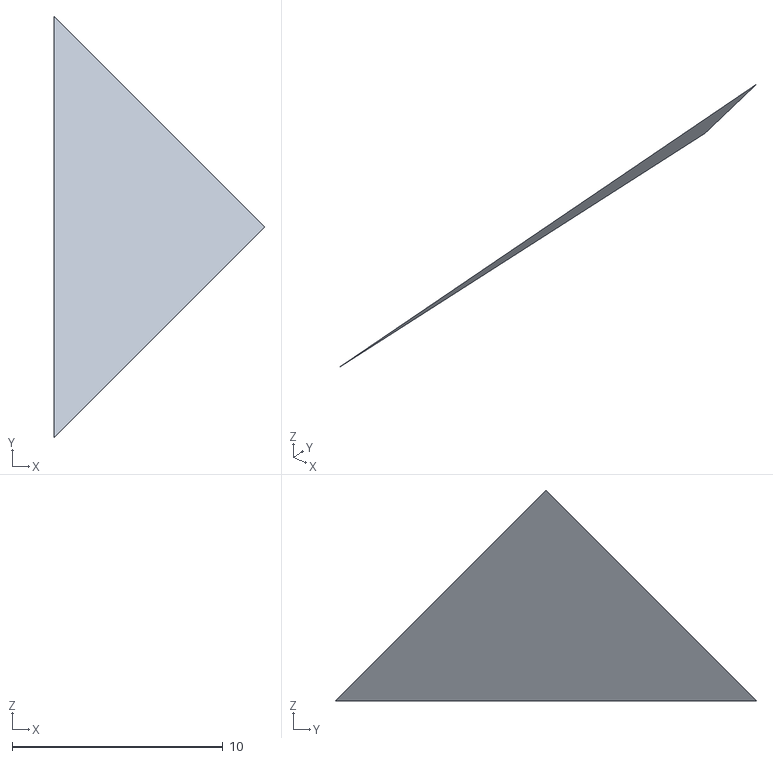
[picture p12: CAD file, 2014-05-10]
ground/tracker/scad_files/out.stl
10.0 x 20.0 x 10.0

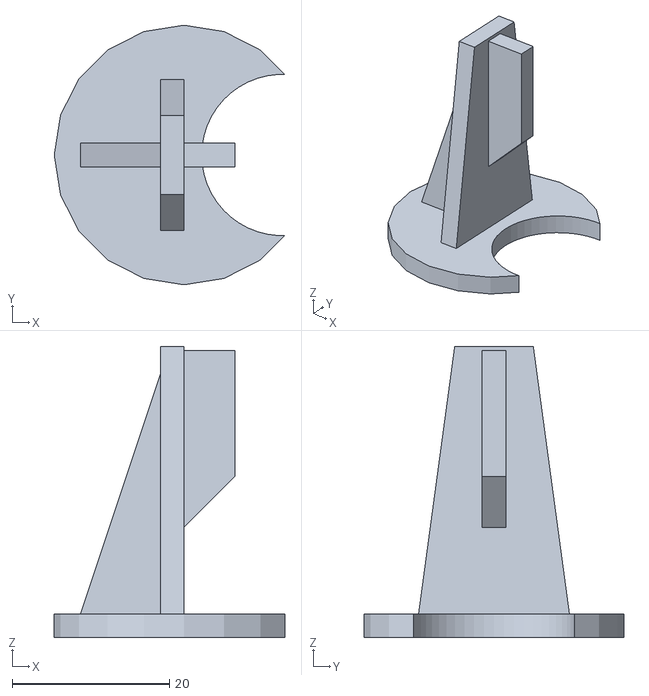
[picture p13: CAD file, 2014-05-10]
ground/tracker/scad_files/output/inner_bearing_bracket.stl
29.3 x 33.0 x 37.0

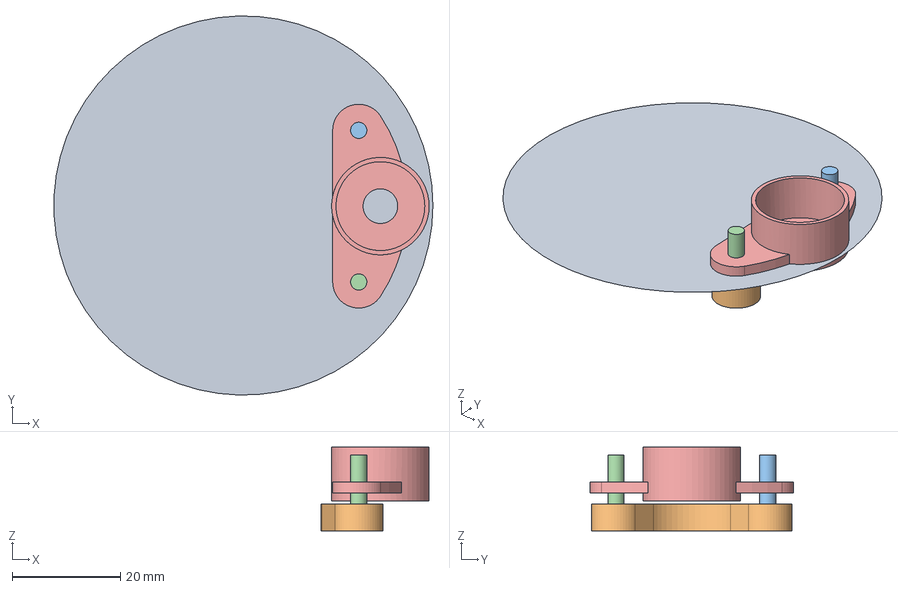
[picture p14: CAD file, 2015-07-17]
ground/tracker/v2/hardware/mechanical/gear_motor_mount.fcstd
70.0 x 70.0 x 15.5 mm
Circle
MotorRetainerNutTrap
BoltCylinderA
BoltCylinderB
MotorTopBracket002

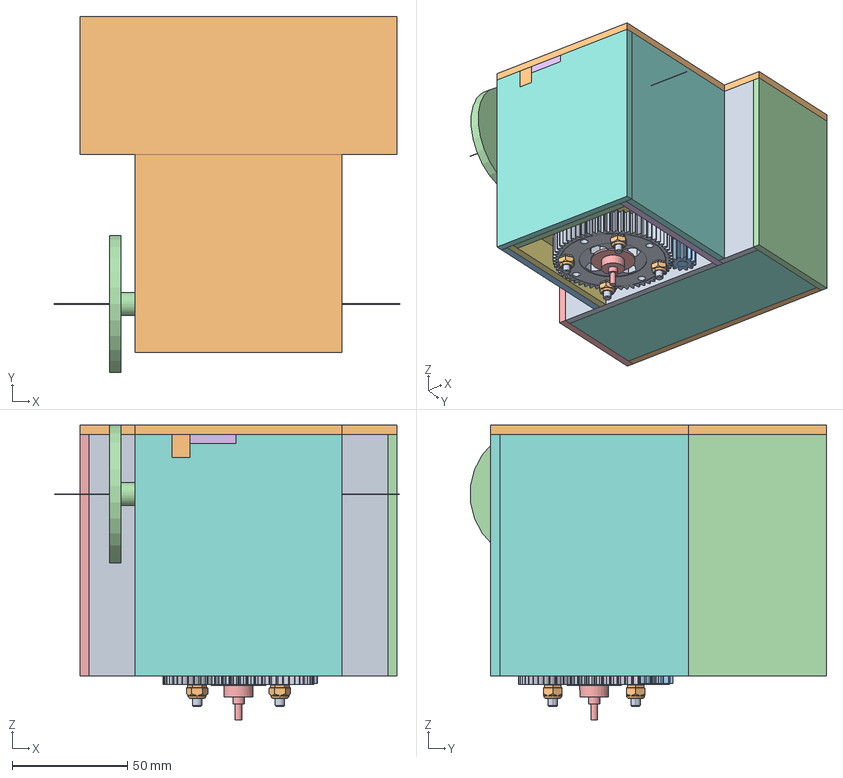
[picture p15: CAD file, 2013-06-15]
hardware/tracker_v1.fcstd
150.0 x 154.8 x 128.2 mm
main_body
nuts
pan_motor
Servo
sliprings
H_bridge
base
front
servo_lug_sup
top_servo_bearer
bottom_servo_bearer
H_bridge_shelf
tilt_axis
STM32F4_Discovery
battery
batbox_base
batbox_batseat
bat_cover
left_side_rect
batbox_right
batbox_left
right_bearer
left_bearer
right_side
batbox_front
top
left_cover_plate
front_bearer
pcb_cover
servo_bearer_brace
batbox_seat_front_bearer
batbox_seat_left_bearer
batbox_seat_right_bearer
h_bridge_support_bearer

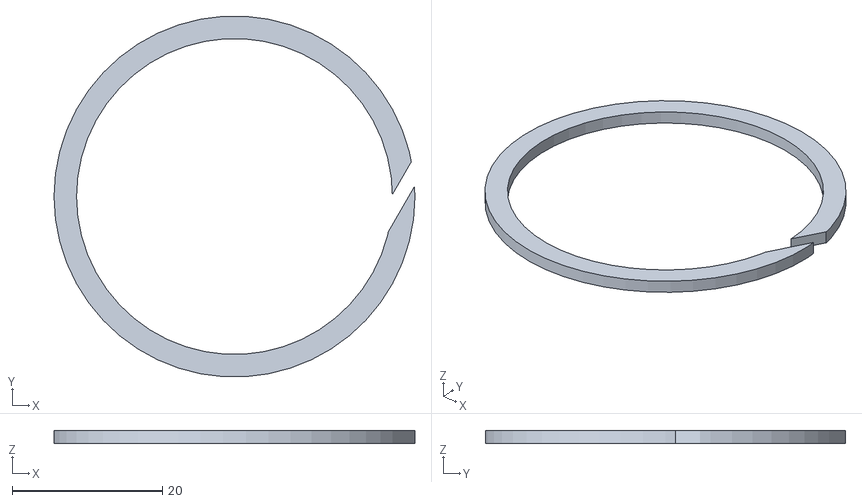
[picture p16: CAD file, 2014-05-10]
ground/tracker/scad_files/output/circlip.stl
48.0 x 47.9 x 1.70

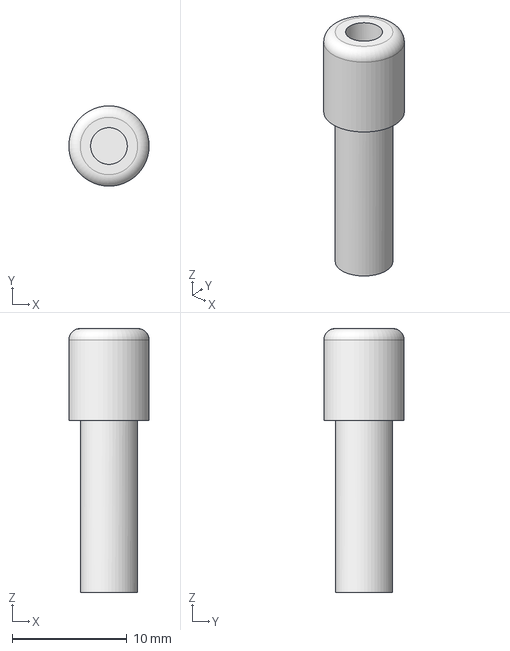
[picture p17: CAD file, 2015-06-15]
ground/tracker/v2/hardware/mechanical/rca_socket.fcstd
6.99 x 7.00 x 23.0 mm

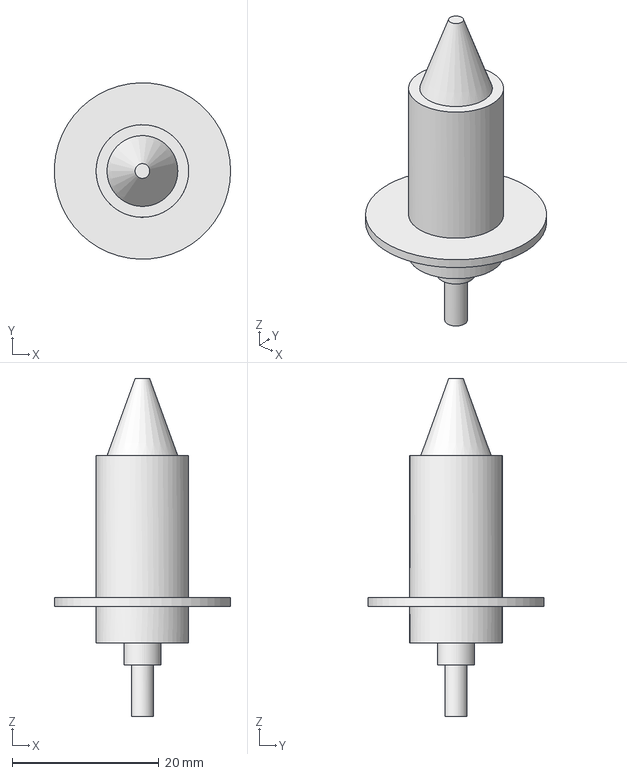
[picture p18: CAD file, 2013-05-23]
hardware/sliprings.fcstd
24.0 x 24.0 x 46.0 mm

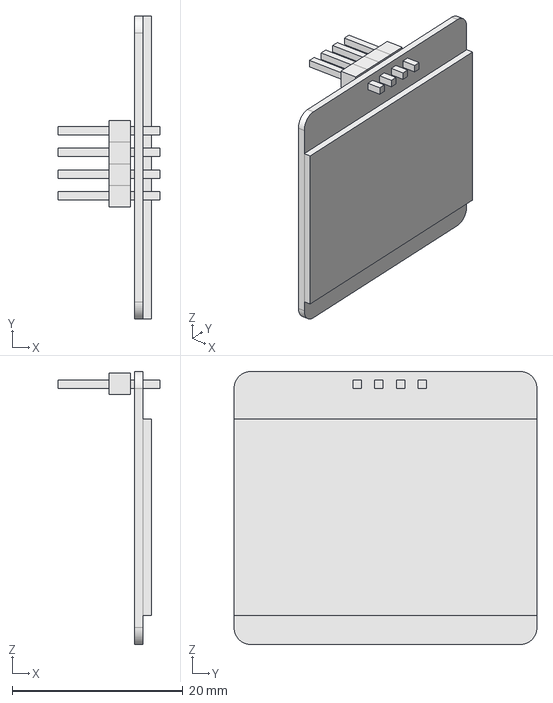
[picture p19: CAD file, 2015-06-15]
ground/tracker/v2/hardware/mechanical/lcd.fcstd
12.0 x 35.5 x 32.0 mm

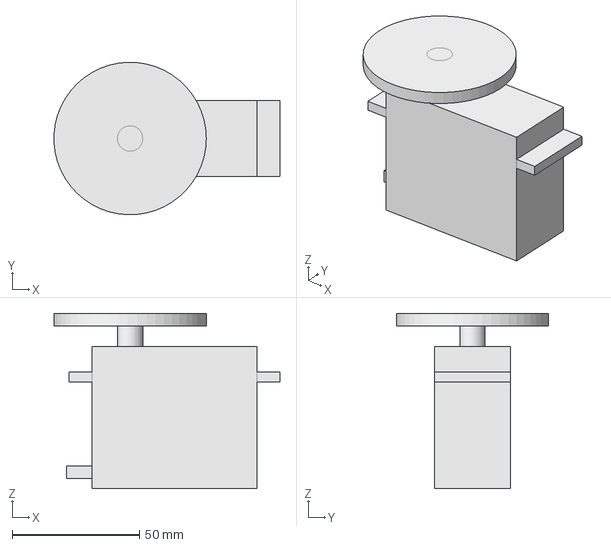
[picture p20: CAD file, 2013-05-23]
hardware/tilt_servo.fcstd
88.9 x 60.0 x 69.0 mm

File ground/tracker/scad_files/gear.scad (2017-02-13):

// Simple Test:
//gear (circular_pitch=700,
//	gear_thickness = 12,
//	rim_thickness = 15,
//	hub_thickness = 17,
//	circles=8);




pi=3.1415926535897932384626433832795;


module gear (
	number_of_teeth=15,
	circular_pitch=false,
	pressure_angle=28,
	clearance = 0.2,
	rim_thickness=6,
	backlash=0,
	twist=0,
	involute_facets=0)
{
	if (circular_pitch==false ) 
		echo("MCAD ERROR: gear module needs a  circular_pitch");

	//Convert diametrial pitch to our native circular pitch
	//circular_pitch = (circular_pitch!=false?circular_pitch:180/diametral_pitch);

	// Pitch diameter: Diameter of pitch circle.
	pitch_diameter  =  number_of_teeth * circular_pitch / 180;
	pitch_radius = pitch_diameter/2;
	//echo ("Teeth:", number_of_teeth, " Pitch diameter:", pitch_diameter);

	// Base Circle
	base_radius = pitch_radius*cos(pressure_angle);

	// Diametrial pitch: Number of teeth per unit length.
	pitch_diametrial = number_of_teeth / pitch_diameter;

	// Addendum: Radial distance from pitch circle to outside circle.
	addendum = 1/pitch_diametrial;

	//Outer Circle
	outer_radius = pitch_radius+addendum;
    echo("outer radius = ", outer_radius);
	// Dedendum: Radial distance from pitch circle to root diameter
	dedendum = addendum + clearance;

	// Root diameter: Diameter of bottom of tooth spaces.
	root_radius = pitch_radius-dedendum;
	backlash_angle = backlash / pitch_radius * 180 / pi;
	half_thick_angle = (360 / number_of_teeth - backlash_angle) / 4;

	// Variables controlling the rim.
	//rim_radius = root_radius - rim_width;

	// Variables controlling the circular holes in the gear.
//	circle_orbit_diameter=hub_diameter/2+rim_radius;
//	circle_orbit_curcumference=pi*circle_orbit_diameter;

				linear_extrude (height=rim_thickness, convexity=10, twist=twist)
				gear_shape (
					number_of_teeth,
					pitch_radius = pitch_radius,
					root_radius = root_radius,
					base_radius = base_radius,
					outer_radius = outer_radius,
					half_thick_angle = half_thick_angle,
					involute_facets=involute_facets);

}

module gear_shape (
	number_of_teeth,
	pitch_radius,    //radius at which  gear teeth make contact
	root_radius,     // 
	base_radius,     // pitch_radius*cos(pressure_angle);
	outer_radius,    //
	half_thick_angle,  //
	involute_facets)   //number of facets?
{
	union()
	{
		rotate (half_thick_angle) circle ($fn=number_of_teeth*2, r=root_radius);

		for (i = [1:number_of_teeth])
		{
			rotate ([0,0,i*360/number_of_teeth])
			{
				involute_gear_tooth (
					pitch_radius = pitch_radius,
					root_radius = root_radius,
					base_radius = base_radius,
					outer_radius = outer_radius,
					half_thick_angle = half_thick_angle,
					involute_facets=involute_facets);
			}
		}
	}
}

module involute_gear_tooth (
	pitch_radius,
	root_radius,
	base_radius,
	outer_radius,
	half_thick_angle,
	involute_facets)
{
	min_radius = max (base_radius,root_radius);

	pitch_point = involute (base_radius, involute_intersect_angle (base_radius, pitch_radius));
	pitch_angle = atan2 (pitch_point[1], pitch_point[0]);
	centre_angle = pitch_angle + half_thick_angle;

	start_angle = involute_intersect_angle (base_radius, min_radius);
	stop_angle = involute_intersect_angle (base_radius, outer_radius);

	res=(involute_facets!=0)?involute_facets:($fn==0)?5:$fn/4;

	union ()
	{
		for (i=[1:res])
		{
			point1=involute (base_radius,start_angle+(stop_angle - start_angle)*(i-1)/res);
			point2=involute (base_radius,start_angle+(stop_angle - start_angle)*i/res);
				side1_point1=rotate_point (centre_angle, point1);
				side1_point2=rotate_point (centre_angle, point2);
				side2_point1=mirror_point (rotate_point (centre_angle, point1));
				side2_point2=mirror_point (rotate_point (centre_angle, point2));

				polygon (
					points=[[0,0],side1_point1,side1_point2,side2_point2,side2_point1],
					paths=[[0,1,2,3,4,0]]);

		}
	}
}

// Mathematical Functions
//===============

// Finds the angle of the involute about the base radius at the given distance (radius) from it's center.
//source: http://www.mathhelpforum.com/math-help/geometry/136011-circle-involute-solving-y-any-given-x.html

function involute_intersect_angle (base_radius, radius) 
	= sqrt (pow (radius/base_radius, 2) - 1) * 180 / pi;

// Calculate the involute position for a given base radius and involute angle.

function rotated_involute (rotate, base_radius, involute_angle) = 
[
	cos (rotate) * involute (base_radius, involute_angle)[0] 
		+ sin (rotate) * involute (base_radius, involute_angle)[1],
	cos (rotate) * involute (base_radius, involute_angle)[1] 
		- sin (rotate) * involute (base_radius, involute_angle)[0]
];

function mirror_point (coord) = 
[
	coord[0], 
	-coord[1]
];

function rotate_point (rotate, coord) =
[
	cos (rotate) * coord[0] + sin (rotate) * coord[1],
	cos (rotate) * coord[1] - sin (rotate) * coord[0]
];

function involute (base_radius, involute_angle) = 
[
	base_radius*(cos (involute_angle) + involute_angle*pi/180*sin (involute_angle)),
	base_radius*(sin (involute_angle) - involute_angle*pi/180*cos (involute_angle)),
];

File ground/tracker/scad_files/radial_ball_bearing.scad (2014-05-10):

include <MCAD/materials.scad>
include <MCAD/math.scad>
include <slipring12Wire.scad>

module radial_ball_bearing(
	od,bore,thickness
   
){
  ring_width =( od - bore) /3;
  ball_dia = (od-bore)/4;
  groove_dia = (od + bore)/2;
  groove_circum = PI * groove_dia;
  num_balls = floor( groove_circum / ( 2 * ball_dia) );
  translate([0,0,-thickness/2]){
	  Ring(od,od-ring_width,thickness);
	  Ring(bore+ring_width,bore,thickness);
  }
  for(i=[0:num_balls -1]){
		rotate((360 / num_balls) * i){
			translate([ groove_dia / 2,0,0]){
				sphere(d=ball_dia, $fn = 10);
			}
		}
	}

  module Ring(outerD,innerD,thickness){
 epsilon = 0.1;
	difference(){
		cylinder(h = thickness, d=outerD , $fn= 20) ;
		translate([0,0,-epsilon]){
	   	  cylinder(h = thickness + 2 * epsilon, d=innerD, $fn= 20);
	   }
   }
}
}

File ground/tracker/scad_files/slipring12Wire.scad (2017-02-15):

module slipring()
{
	union(){
		translate ([0,0,-25.5 + 5 + 1.2]){
			cylinder(h = 25.5, d = 12.6, $fn = 30);
		}

		translate([0,0,1.2 + 5]){
			cylinder (h = 3, d = 5,$fn = 12);
		}
	} // union 
}

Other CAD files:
ground/tracker/scad_files/output/motor_mount.stl
ground/tracker/v2/hardware/mechanical/db9.fcstd
hardware/turntable.fcstd
ground/tracker/scad_files/output/pinion.stl
ground/tracker/scad_files/gear_shape.scad
ground/tracker/scad_files/gear_test.scad
ground/tracker/scad_files/output/ballrace_blank.stl
ground/tracker/scad_files/output/inner_bearing_holder_p2.stl
ground/tracker/scad_files/output/outer_bearing_holder_p2.stl
ground/tracker/scad_files/surface.scad
ground/tracker/scad_files/test.scad
ground/tracker/scad_files/tracker_small.scad
ground/tracker/v2/hardware/mechanical/16mm_gear_motor.fcstd
ground/tracker/v2/hardware/mechanical/3_5mm_jack_socket.fcstd
ground/tracker/v2/hardware/mechanical/HD-1501MG-servo.fcstd
ground/tracker/v2/hardware/mechanical/antenna_mount.fcstd
ground/tracker/v2/hardware/mechanical/ballrace.stl
ground/tracker/v2/hardware/mechanical/ballrace30x42x7.fcstd
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

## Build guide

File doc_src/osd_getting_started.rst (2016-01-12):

`OSD Index`_

============================================
Getting started with the Quantracker Air OSD
============================================

----------------
The Board layout
----------------

The board is entirely Open Source hardware and software.
`The V2.2 pcb is currently available at OSHPark`_ .
`The full schematic is available here as a set of pdfs`_ .
`The source code is available on GitHub`_ .

  

The above diagram highlights the connections of the board [1]_. 
 
The initial `board firmwares`_ are designed to be used with Ardupilot and
the layout of the board connectors is designed to be compatible with MinimOSD [2]_ .
The 6 pin header at the right hand end of the diagram is 
used for the MAVLink serial connection, for communicating setup parameters and to flash
firmware onto the board. 
The Header at the left end is used for connecting the Camera
and the Video transmitter [3]_ .  Power to the video transmitter and camera is provided at the breakout pins
labelled VIDI+IN and VIDO+In respectively. (There is a schottky diode on each from the input to the output, so
expect around 0.5 V voltage drop ).

The 2 pin header labelled prog is used to put the board in programming mode.

The board firmware automatically detects PAL and NTSC cameras, 
or the board will output white symbology on a black background if no camera signal is present.

For more info , please look at the `OSD index`_.

.. _`OSD Index`: osd/index.html
.. _Index: index.html
.. _`see the mcu schematic`: https://github.com/kwikius/quantracker/blob/master/air/osd/hardware/64_pin_lite/air_osd_v1/schematic_pdf/osd-MCU.pdf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
.. _`The full schematic is available here as a set of pdfs`: https://github.com/kwikius/quantracker/blob/master/air/osd/hardware/64_pin_lite/air_osd_v2_1/schematic_pdf
.. _`The V2.2 pcb is currently available at OSHPark`: https://oshpark.com/shared_projects/PtiEsgAu
.. _`The source code is available on GitHub`: https://github.com/kwikius/quantracker
.. _`board firmwares`: osd/firmwares.html
.. _`The board has the capability to be a full Flight controller with onboard OSD`: https://www.youtube.com/watch?v=KQLArFbRjWg
                                               
.. [1] There are many other available pins, which are broken out from
       the STM32F4 processor. For a more complete view of the functions 
       on the board `see the mcu schematic`_. 
       (`The board has the capability to be a full Flight controller with onboard OSD`_ ).

.. [2] There are minor differences.

.. [3] The output to the Video transmitter also provides 2 buffered Audio channels. 
       Options include sending FSK telemetry data, audio variometer, voice alerts etc.

`OSD Index`_

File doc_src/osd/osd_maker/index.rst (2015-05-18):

`Quantracker Index`_

`OSD Index`_

---------------------
Quantracker OSD_maker
---------------------

This App can be used to create custom OSD displays 
from the Quantracker Air OSD board.

The App can import, create and modify Bitmaps and Fonts 
and convert them into source code which can be linked in 
to provide highly customisable resources for your Application.

To provide easy access to Fonts and bitmaps, the App stores them 
as png files, so as well as being modifiable within osd_maker, they can also be
manipulated in your favourite bitmap editor

As well as manipulating raw resources, the App can be used to
show a very accurate mock up of the display as it will appear on the OSD.

-------------
Some features
-------------

   *  Import image files in standard formats
   *  Import mcm (font) files from MinimOSD
   *  Output source code and firmware
   *  Setup parameters of firmware

.. _`Quantracker Index`: ../index.html
.. _`OSD Index`: ../index.html

`OSD Index`_

`Quantracker Index`_

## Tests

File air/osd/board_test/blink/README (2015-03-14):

To program 
stm32flash -f -v -w blink.bin /dev/ttyUSB0

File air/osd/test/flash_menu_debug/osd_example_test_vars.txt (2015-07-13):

set frsky_invert_telem true
set show_home true
set osd_home_pos [-160,70,60]
set show_compass true
set osd_compass_pos [0,-117,-65]
set show_altitude true
set osd_altitude_pos [-160,50,40]
set show_gps_no_fix false
set osd_gps_no_fix_pos [-100,50,30]
set show_afcl_horizon true
set osd_afcl_horizon_pitch_adj 0

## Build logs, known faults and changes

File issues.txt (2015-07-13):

Fri Jul 10 10:56:59 BST 2015
If you get errors from the quan library (GitHub/kwikius/quan-trunk ) then try downloading the current master branch.
Though this librray is relatively stable, I am still working on it so some projects will need the latest version.

Mon 18 May 2015 15:17:59 BST 
If you get error messages from the baord  when writing in the flash menu. It may be due to an old version of the libraries
Currently the libraries amake files are in air/osd/ dir so object files dont all get remade for different flags etc.
Also After building a particular library, do 'make clean' or rm *.o to remove any object files which may cause a problem.
TODO move all this stuff out of there!

Mon 18 May 2015 15:17:45 BST 
If set up as transmitter or receiver then OSD hangs if you dont
add receive_telemetry_task etc. A common issue with freertos where Semaphores are called without being inialised
also need local rx_telemtry stuff. Overall needs thought as to how it should work.
maybe should be folded into draw_task. Anyway needs documentation. Probably should be C++ classes.
TODO looh at mbed rtos and see if an be made compat. Unfortunately the stm32 standard libraries are quite slow
though

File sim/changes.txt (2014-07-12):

4 Aug 2013
changed panel in panel.*pp to derive from wxScrolledWindow so it can be scrolled if too large for screen

Moved aircraft gps to separate file

----------------

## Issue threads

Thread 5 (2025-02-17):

only armed/no arm and mode changes

easytake, 2025-02-17:
Hi,
I made OSD board v2.2 and build the example code to the board,
but it only armed/no arm and mode changes.
any ideas?

The wiring diagram is attached.

Vic

[test.pdf](https://github.com/user-attachments/files/18817476/test.pdf)

Closed 2025-02-26.

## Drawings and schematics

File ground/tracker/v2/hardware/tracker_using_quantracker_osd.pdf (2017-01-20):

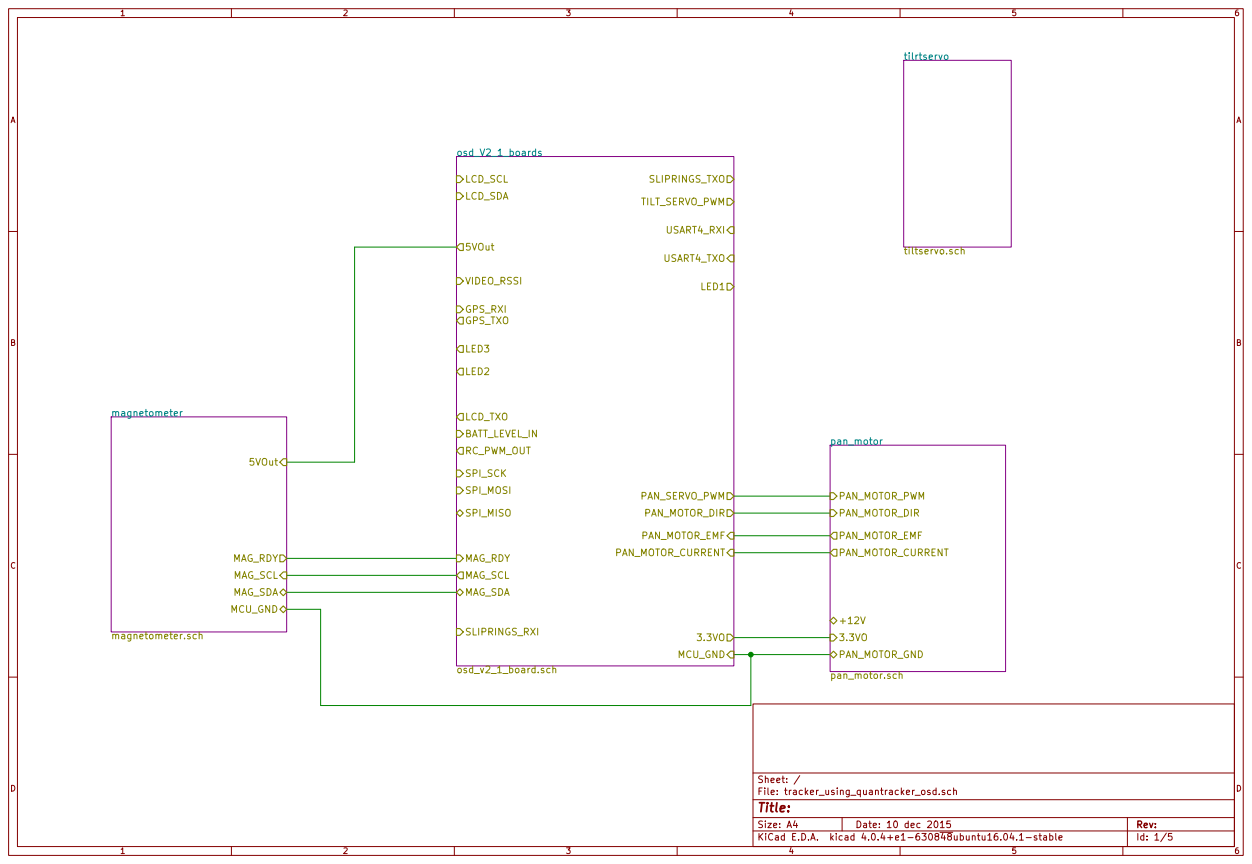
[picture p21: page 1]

File: tracker_using_quantracker_osd.sch Sheet: / magnetometer

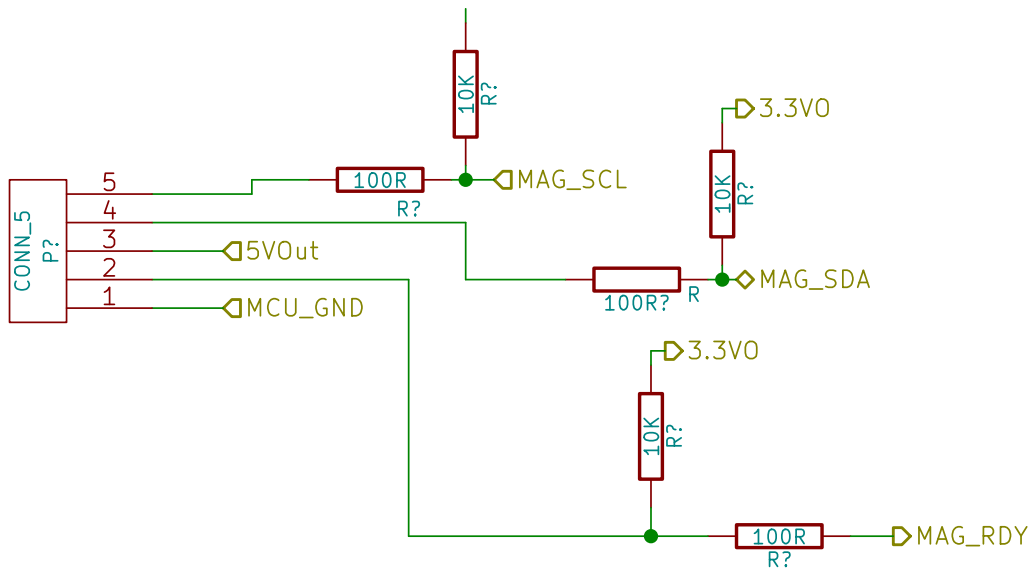
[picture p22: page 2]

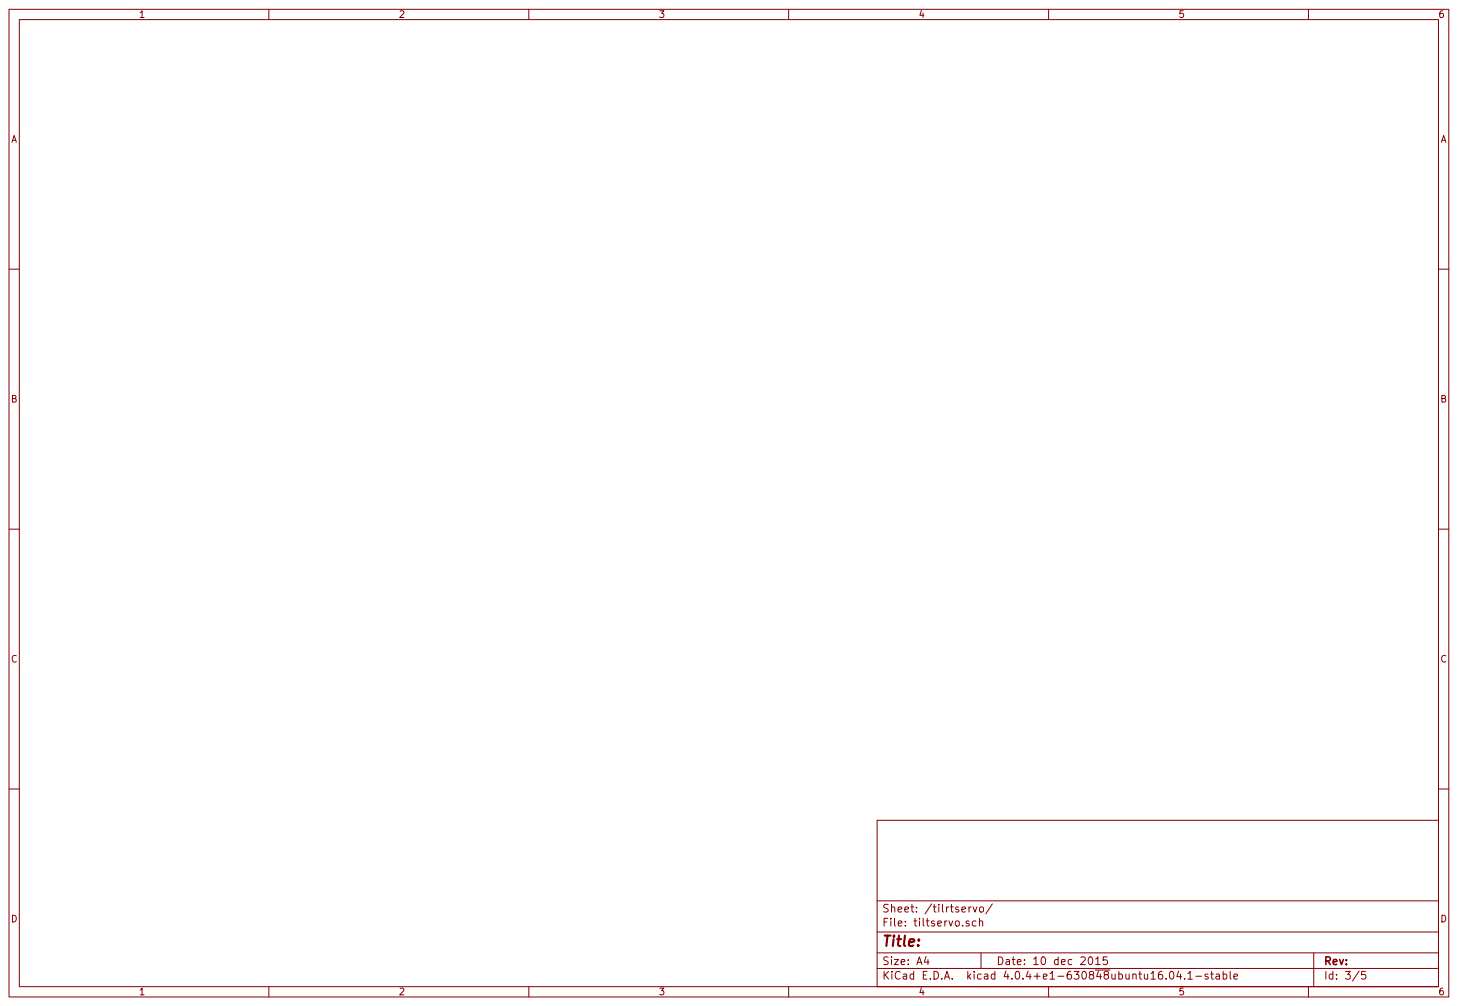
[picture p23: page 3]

Id: 3/5 Title: File: tiltservo.sch Sheet: /tilrtservo/

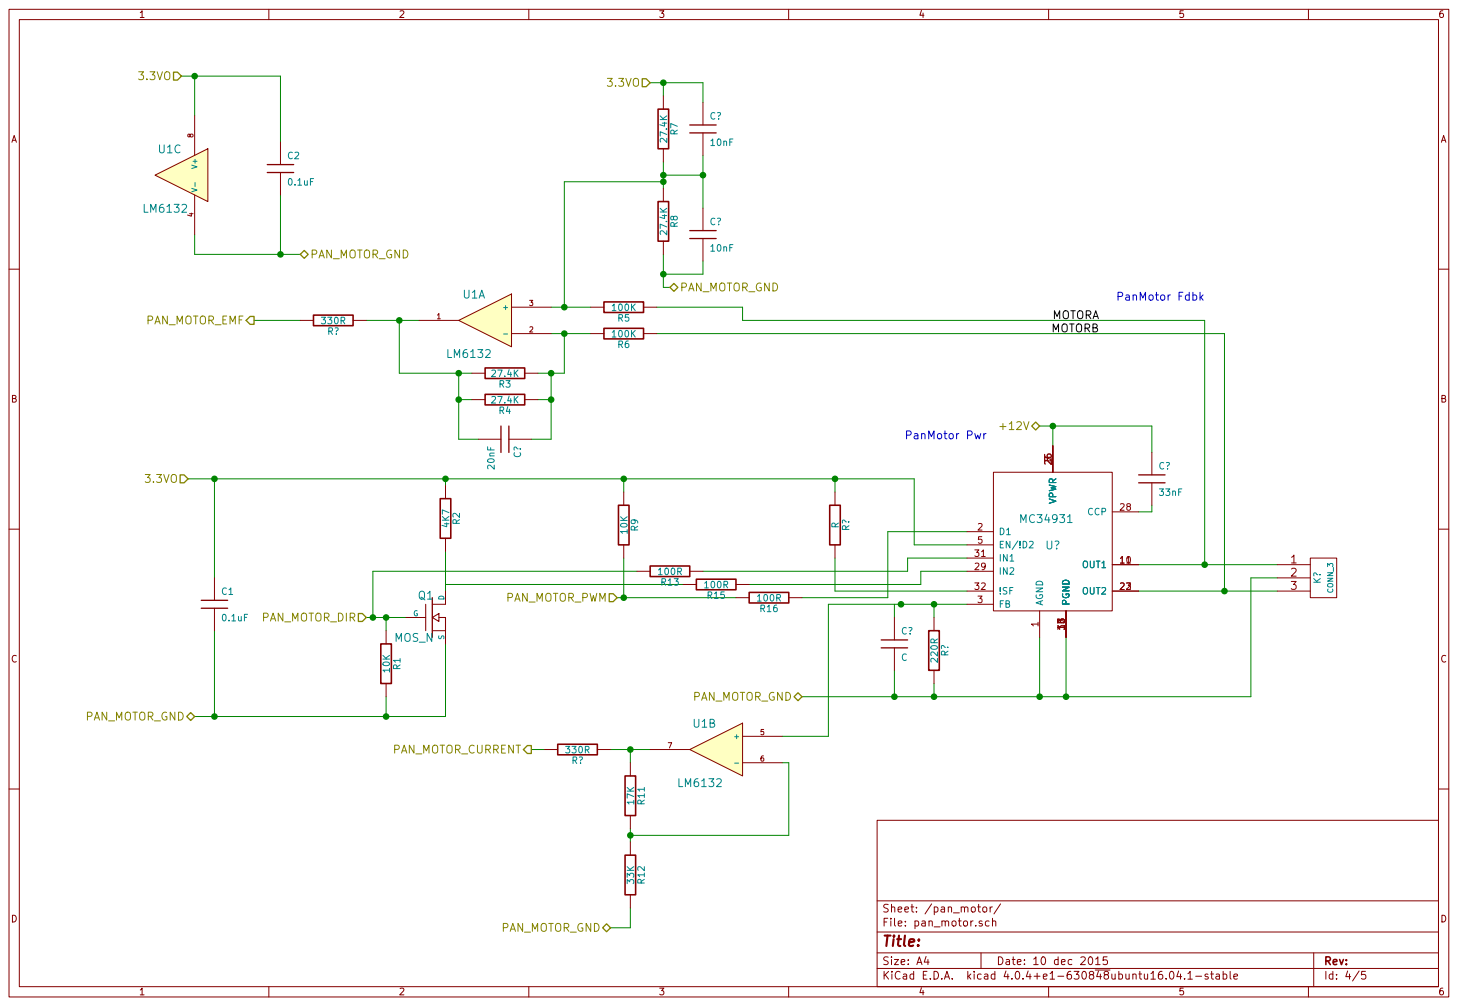
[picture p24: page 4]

PanMotor Fdbk PanMotor Pwr

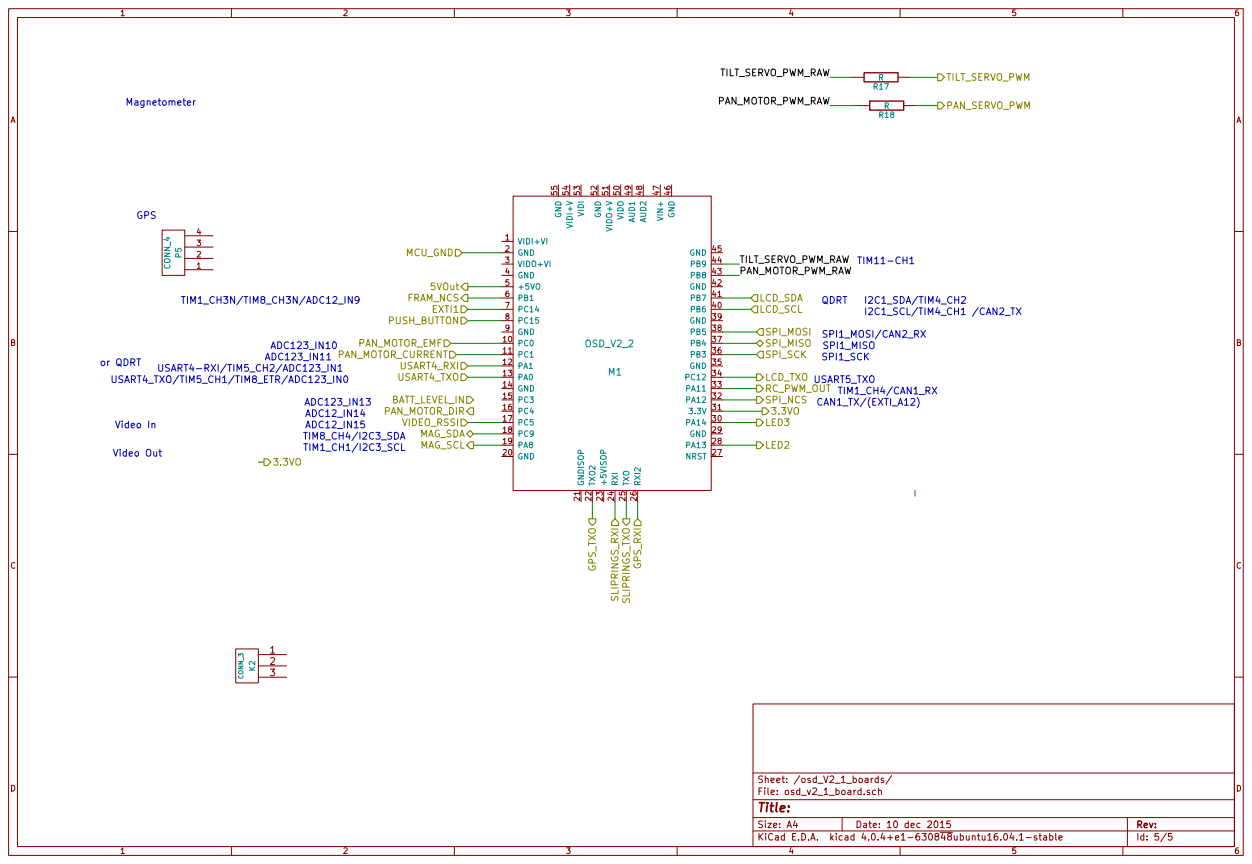
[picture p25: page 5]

R17 R Video Out Video In GPS

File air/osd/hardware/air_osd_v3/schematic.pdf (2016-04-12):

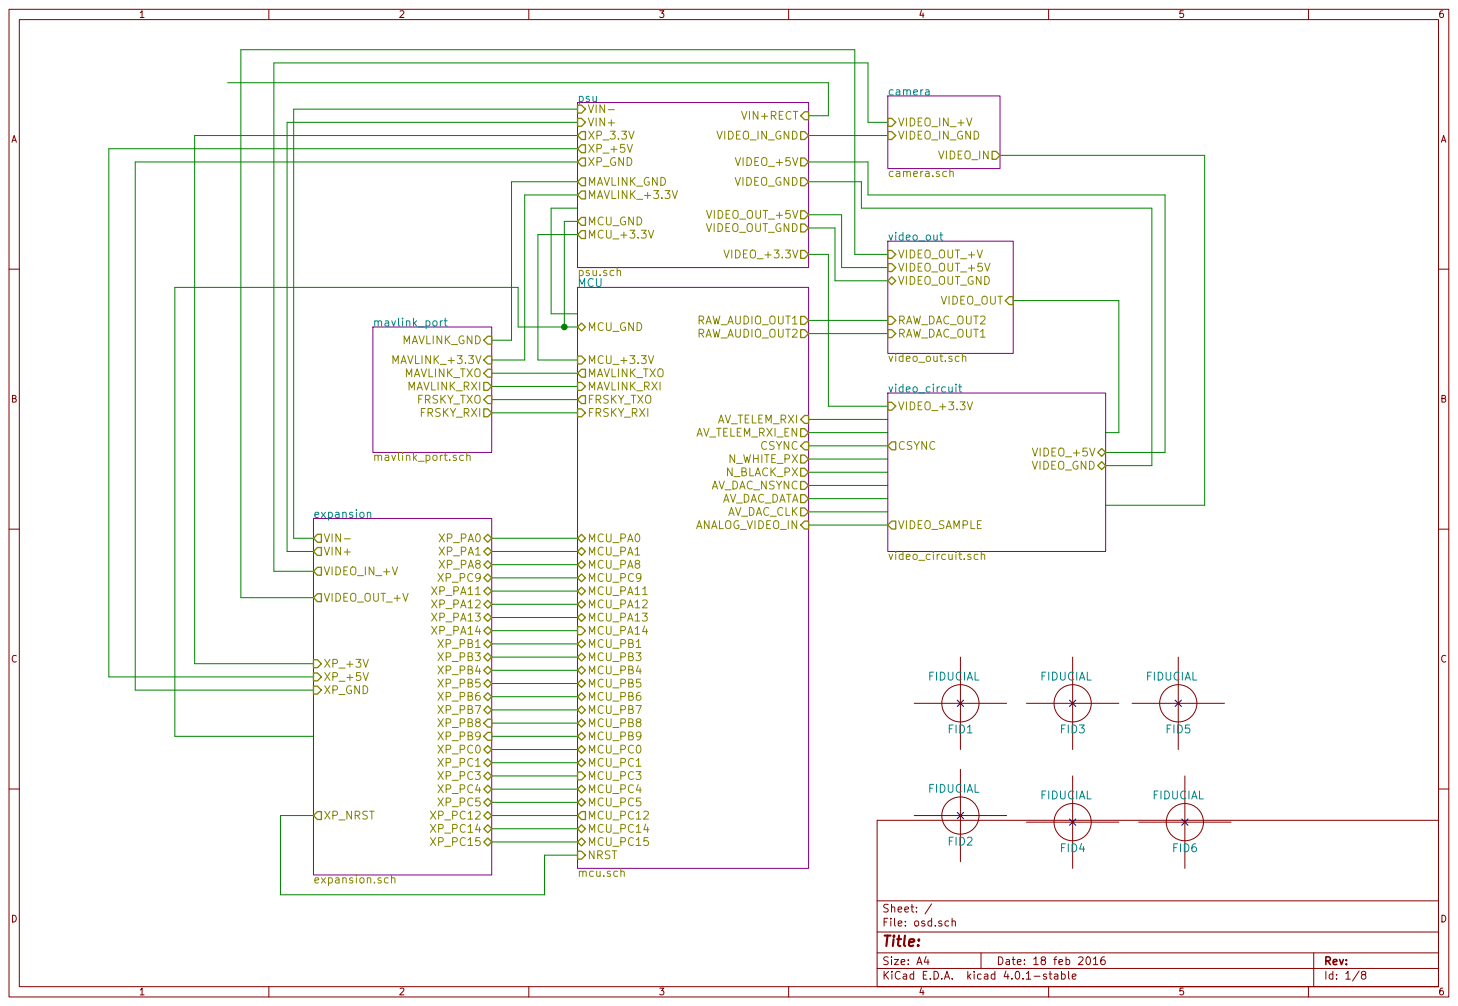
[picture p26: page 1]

mavlink_port expansion

MAVLINK_GND MAVLINK_+3.3V MAVLINK_TXO

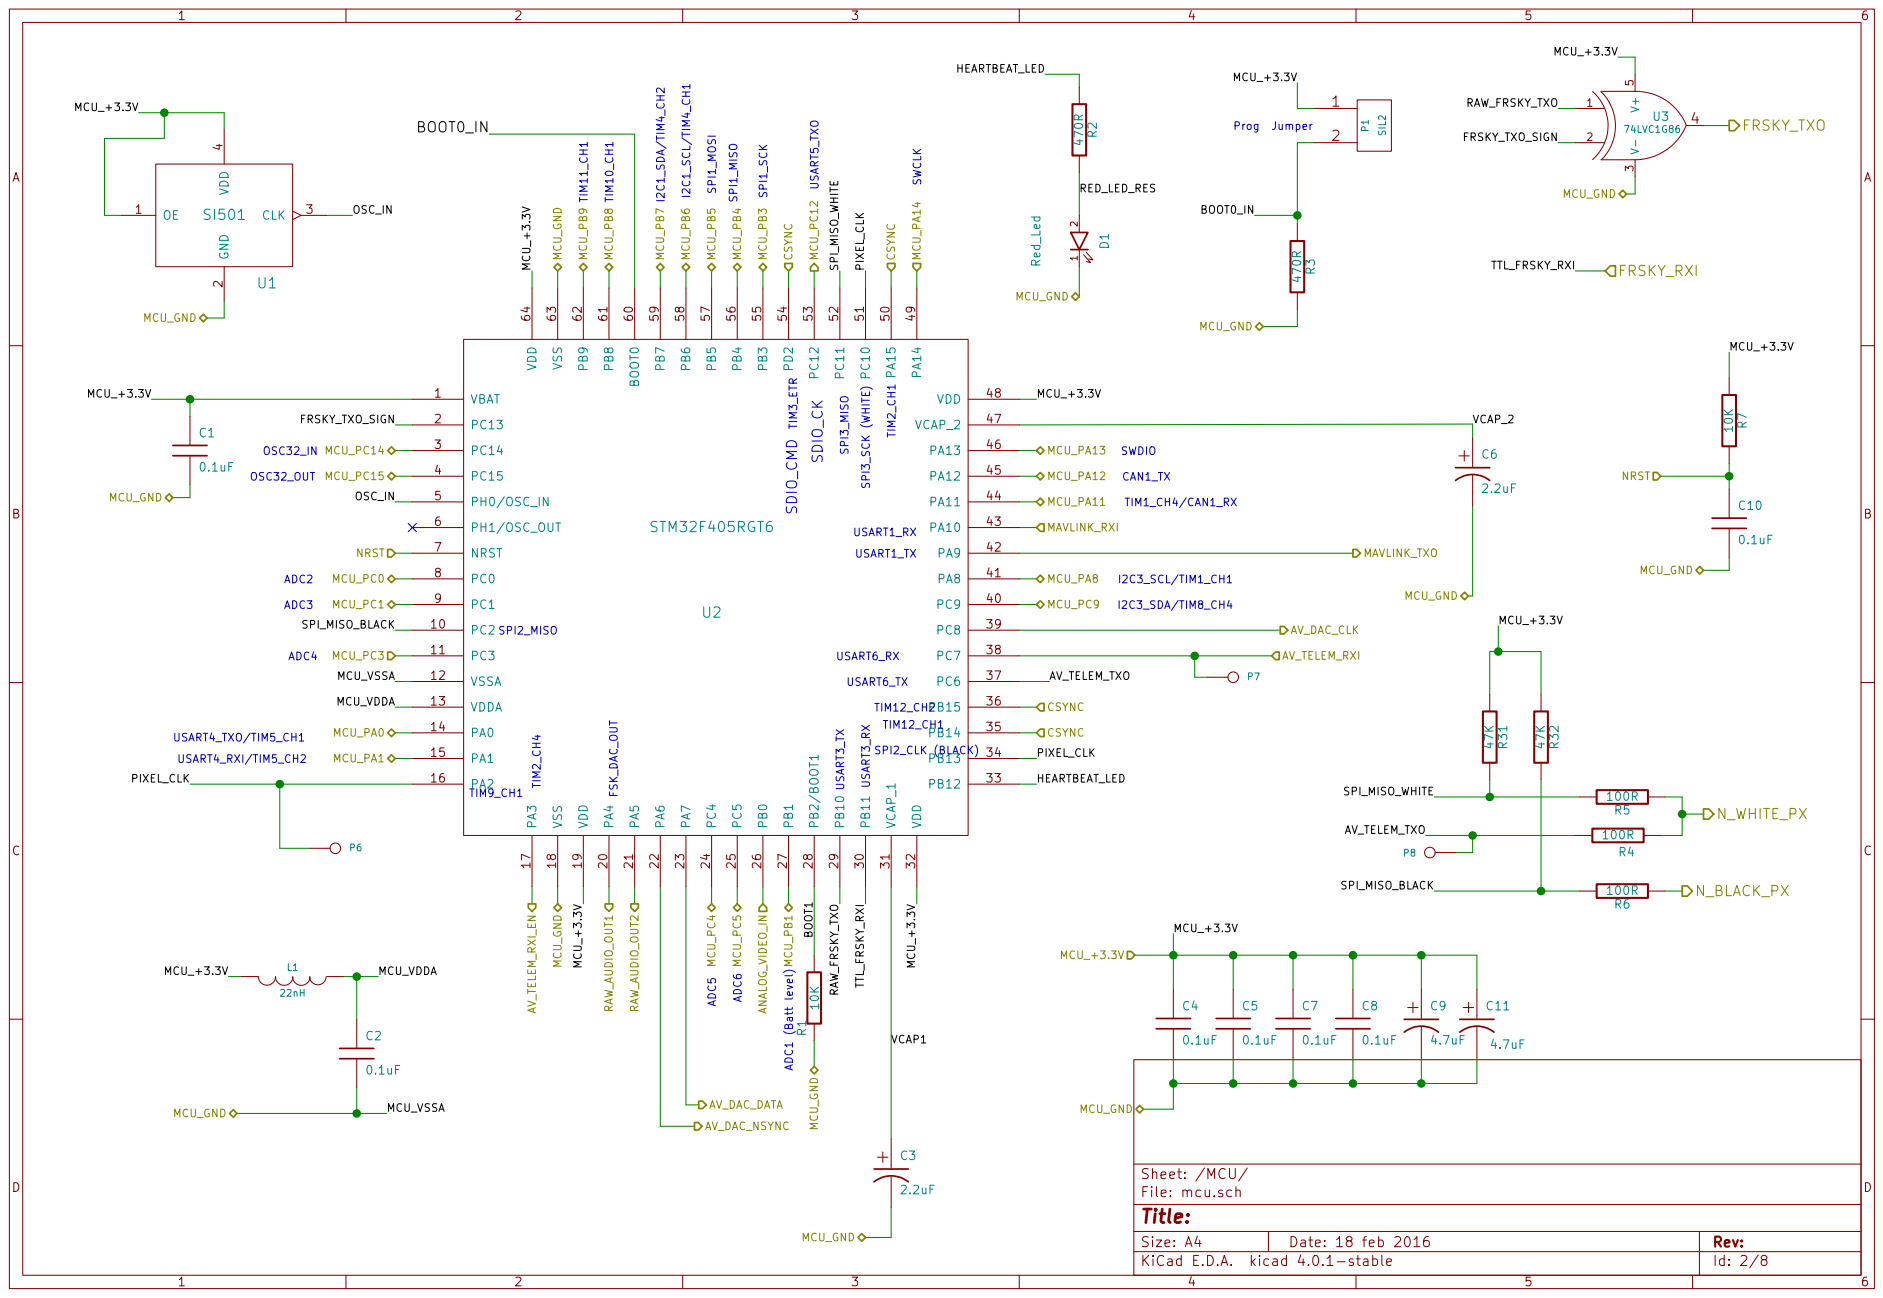
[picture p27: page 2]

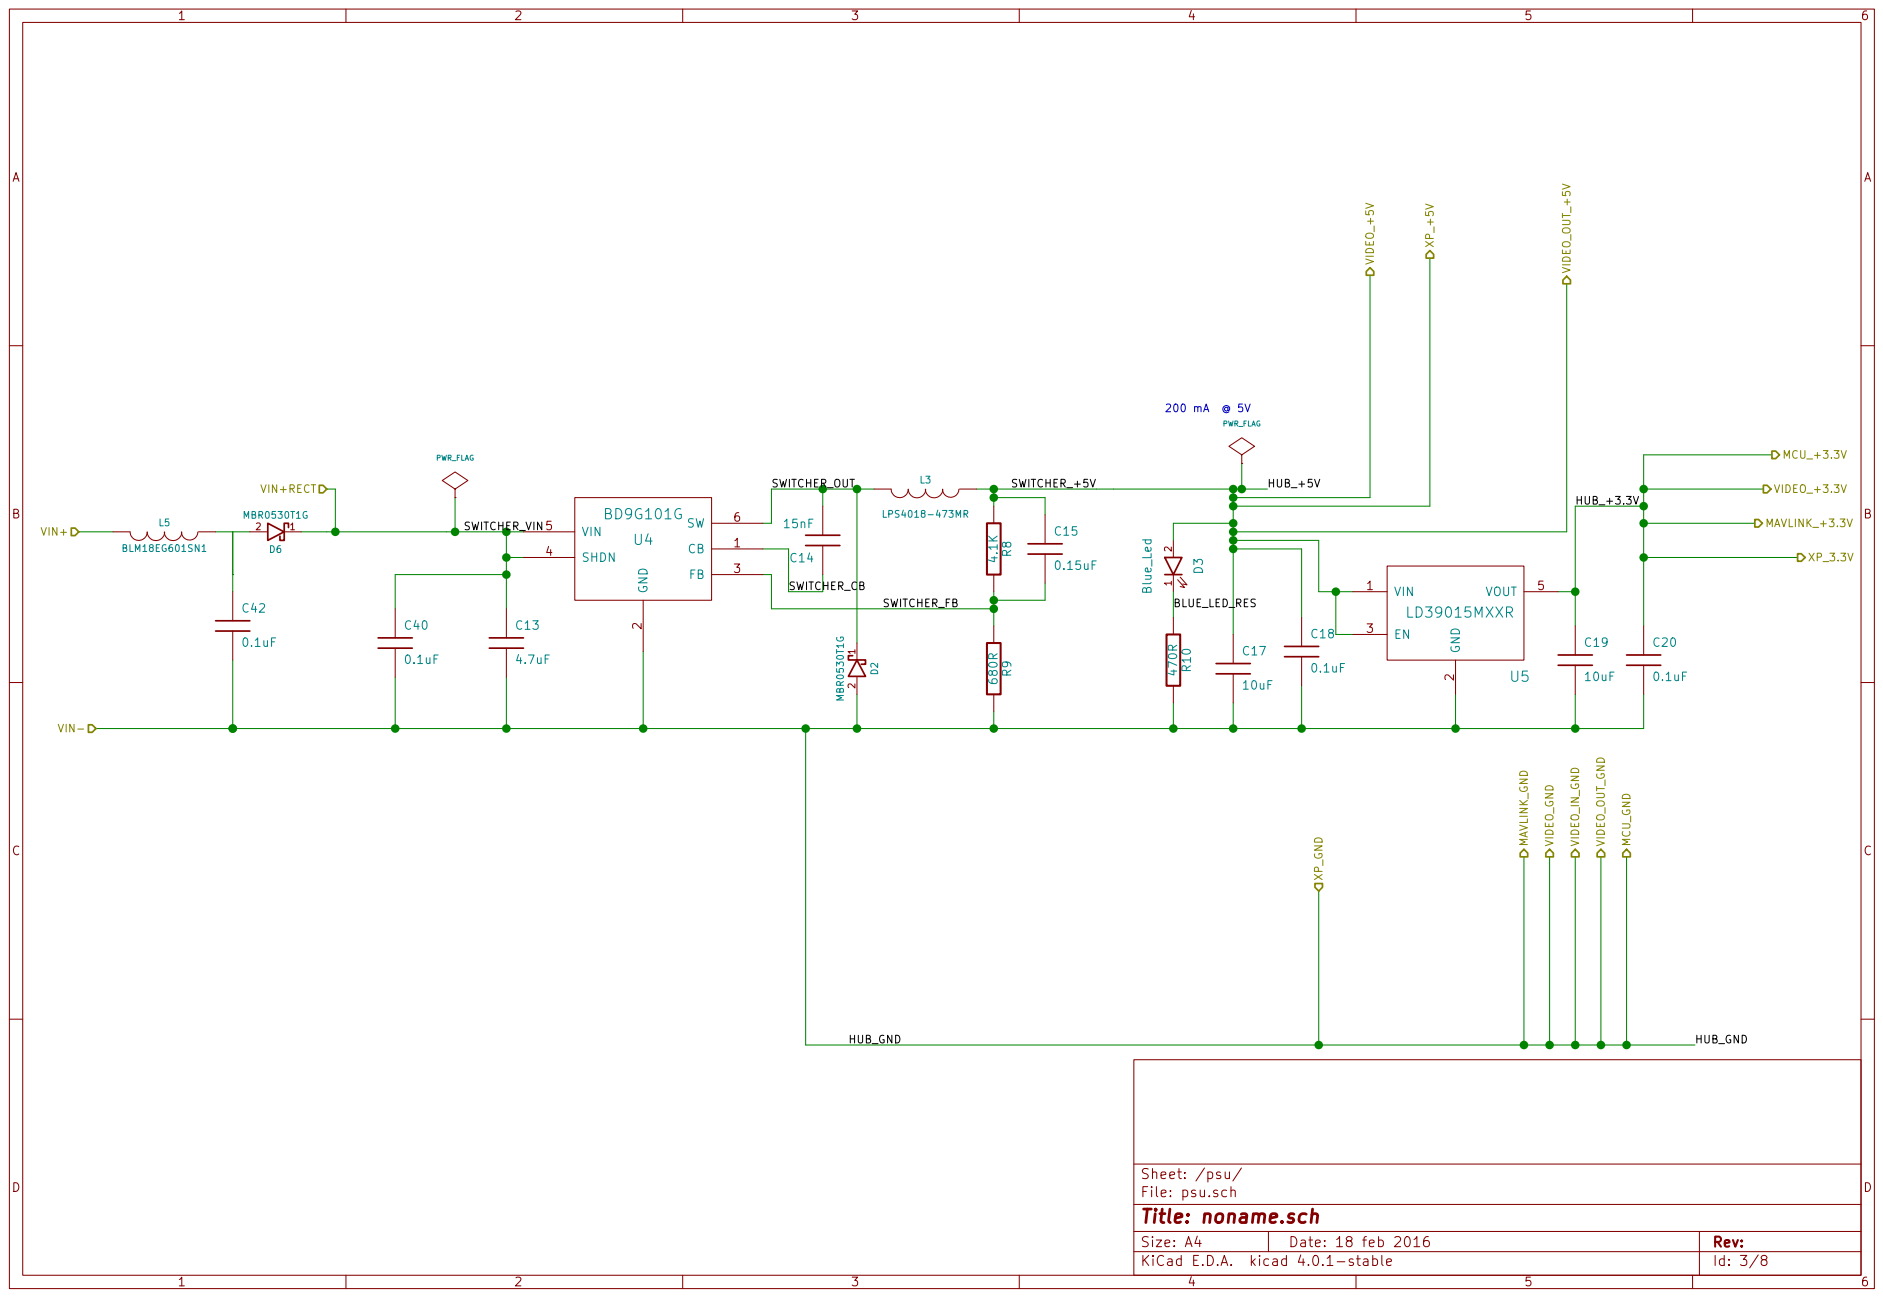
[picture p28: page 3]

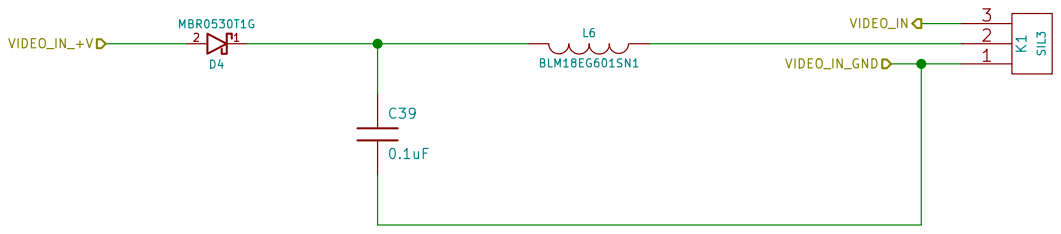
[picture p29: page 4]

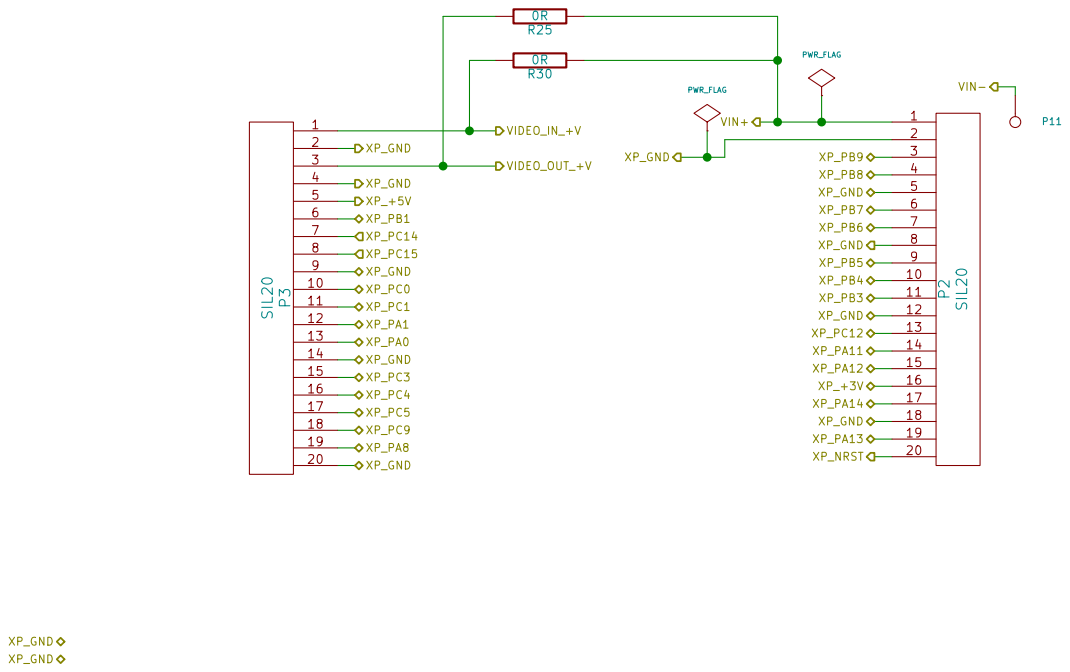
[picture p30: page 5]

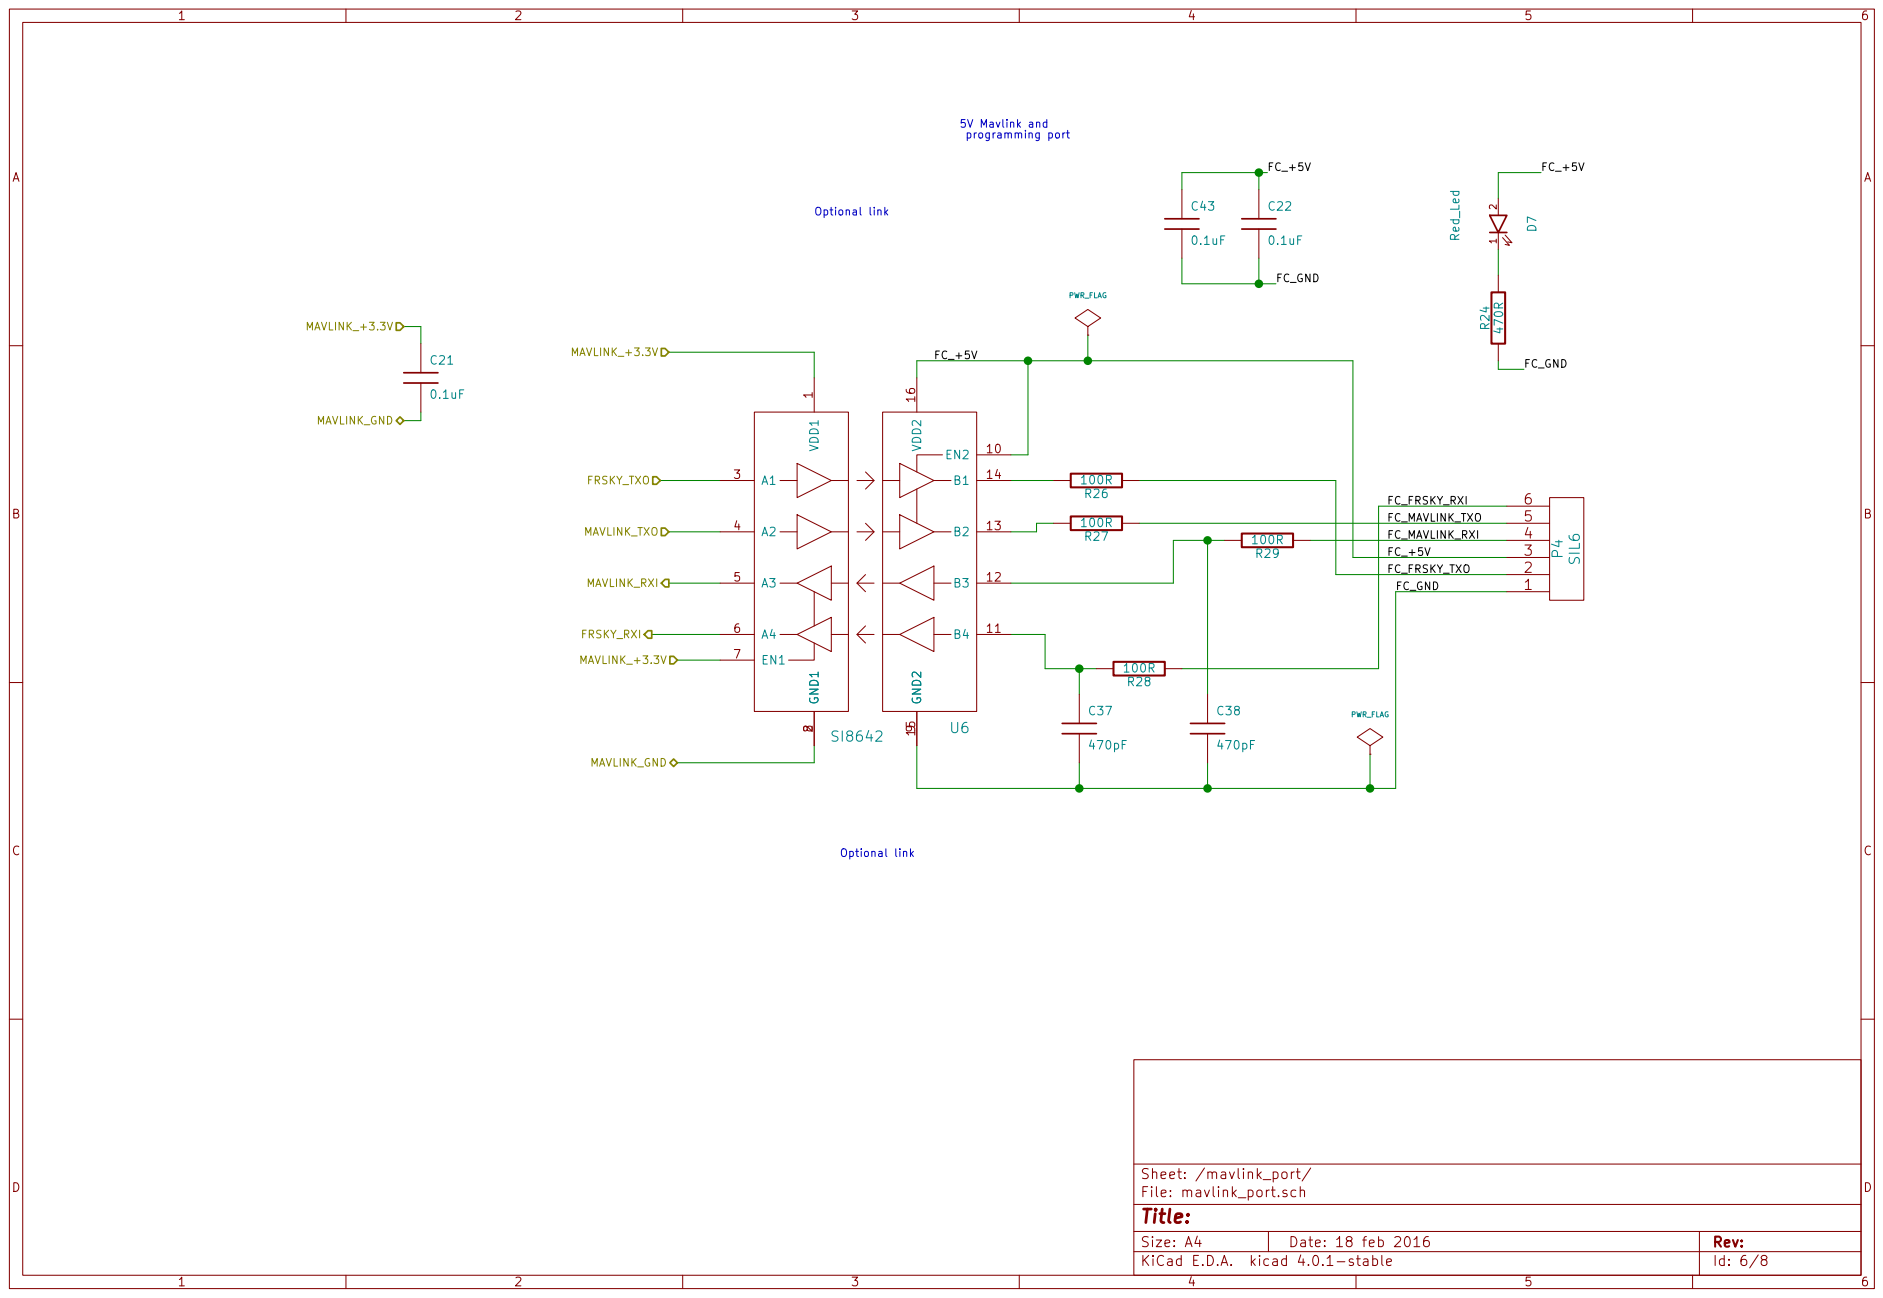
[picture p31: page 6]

4 FC_MAVLINK_RXI
FC_+5V 3

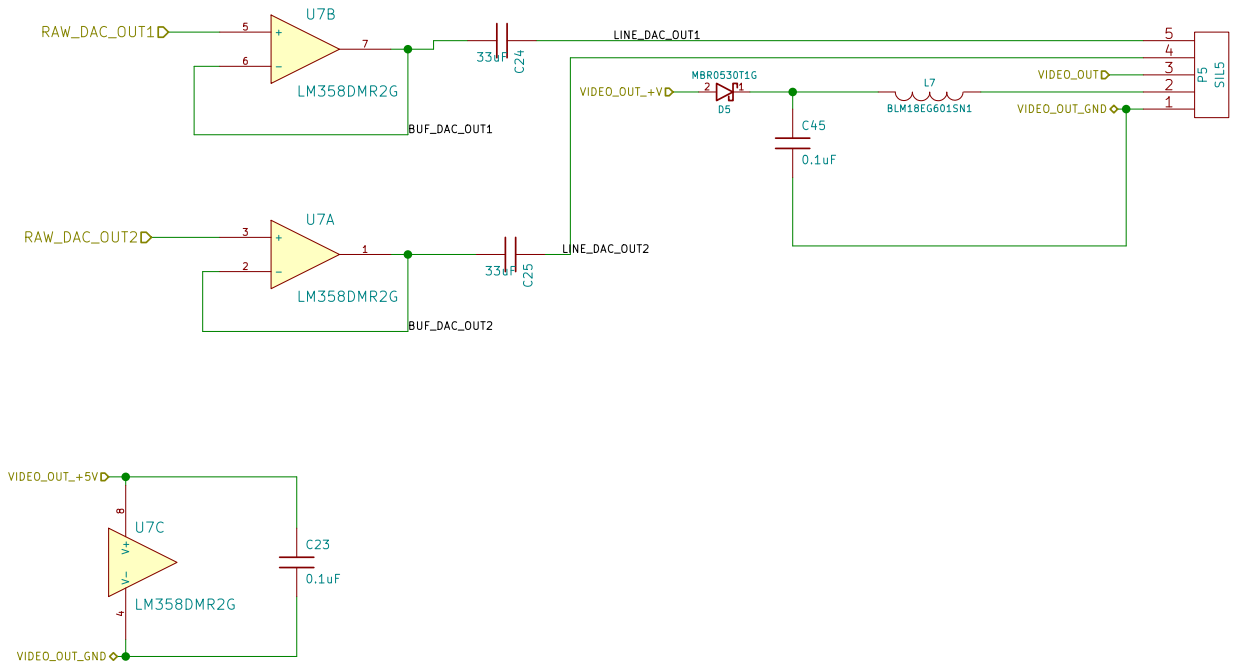
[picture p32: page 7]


Provide 50 mA on 5V supply

Provide 25 mA on 3V supply

LP filter to remove
4.43361875 MHz
color subcarrier

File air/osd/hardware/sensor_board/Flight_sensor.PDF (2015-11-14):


AUDIO_2 48 AUDIO_1 49 VIDEO_OUT 50 VIDO+V 51 GND 52 VIDEO_IN 53 VIDI+V 54 GND 55

use spi bus reference to the pixhawk
the cs pin in the FM25V01 can be changede by your choice

0ZCA0035FF2G
Filter to the 5V from board to GPS
reference to Pix GPS Connector

console can also be used for programming the bord






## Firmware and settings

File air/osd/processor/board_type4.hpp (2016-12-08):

#ifndef QUANTRACKER_AIR_OSD_PROCESSORS_BOARD_TYPE4_HPP_INCLUDED
#define QUANTRACKER_AIR_OSD_PROCESSORS_BOARD_TYPE4_HPP_INCLUDED

/*
 Copyright (c) 2013 -2016 Andy Little 

 With Grateful Acknowledgements to the prior work of:
   Sami Korhonen(Openpilot.org)
   taulabs ( taulabs.com) 
   brainFPV ( brainfpv.com)
   Thomas Oldbury (super-osd.com)

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
 You should have received a copy of the GNU General Public License
 along with this program. If not, see <http://www.gnu.org/licenses/>
*/

#include <quan/stm32/freertos/freertos_usart_task.hpp>
#include <quan/stm32/freertos/freertos_usart_task_tx_only.hpp>
#include <quan/stm32/serial_port_lite.hpp>
#include <quan/voltage.hpp>
#include <quan/stm32/gpio.hpp>
#include <quan/stm32/spi.hpp>
#include <quan/stm32/tim.hpp>
#include <quan/stm32/usart.hpp>


#define SWDIO_DEBUG_DRAW_TASK 1
#define SWDIO_DEBUG_MAVLINK_TASK 2
#define SWDIO_DEBUG SWDIO_DEBUG_MAVLINK_TASK

//timers used
typedef quan::stm32::tim2                       video_columns_gate_timer;
// tim3 is also used as the internal video mode timer
typedef quan::stm32::tim3                       video_rows_line_counter;
// 
typedef quan::stm32::tim9                       spi_clock_timer;
//Think this could be changed if necessary
// maybe change this to 32 bit timer and leave running for microsecs
typedef quan::stm32::tim12                      sync_sep_timer;

#if !defined(QUAN_AERFLITE_BOARD)
// only used when writing video dac
typedef quan::stm32::tim10                      video_level_dac_irq_timer;
#endif

// not really part of system
typedef quan::stm32::tim6                       fsk_dac_timer;
#if !defined(QUAN_AERFLITE_BOARD)
typedef quan::stm32::tim7                       dac2_timer;
#endif

/*Timers potentially avail for expansion some multiplexed with other functions ( with i/o)
 N.B. Timer1 CH2 could go out on PA9 (currently Mavlink TX via digitally isolated port
 which might make a nice digitally isolated ESC pwm rc output
 PA10 (Mavlink Rx)  could be used for PPMSUM capture on TIM1 CH3 
TIM1_CH1 
TIM1_CH2-3( on 100 pin part)
TIM1_CH4
TIM4_CH1
TIM4_CH2
TIM4_CH3-4 ( on 100 pin part)
TIM4_CH2
TIM5_CH1
TIM5_CH2
TIM8_CH4
TIM10_CH1 
TIM11_CH1 

/expansion 100 pin io
 10 for timers
 6 for usarts
 3 for spi
 6 for i2c
 6 for ADC
 8 gp port
 2 can
-------------------
 total 43 + power + gnd
 abs min 42 -> 48/4 -> 4 * 13 ( 2 rows of 13 * 2) 52
*/
#if !defined(QUAN_AERFLITE_BOARD)
typedef quan::stm32::usart1                     mavlink_usart;
#endif
// usart2 avail for expansion on 100 pin part
// usart4 avail for expansion on all parts
#if !defined(QUAN_AERFLITE_BOARD)
typedef quan::stm32::usart3                     frsky_usart; // maybe inverted but not on f4
typedef quan::stm32::usart6                     av_telem_usart;
#endif
#if defined(QUAN_AERFLITE_BOARD)
typedef quan::stm32::spi1                       imu_spi;
#else
// SPI1 is available for expansion
#endif

typedef quan::stm32::spi2                       video_mux_out_black_spi;
typedef quan::stm32::spi3                       video_mux_out_white_spi;
// I2C1 I2C2 and I2C3 avail for expansion
//----PORTA---------------------------------------
#if defined(QUAN_AERFLITE_BOARD)
typedef quan::mcu::pin<quan::stm32::gpioa,0>    usart4_txo_pin ;// USART4_TX
typedef quan::mcu::pin<quan::stm32::gpioa,1>    usart4_rxi_pin; // USART4_RX
#endif
#if !defined(QUAN_AERFLITE_BOARD)
typedef quan::mcu::pin<quan::stm32::gpioa,2>    video_spi_clock;// TIM9_CH1
typedef quan::mcu::pin<quan::stm32::gpioa,3>    telem_cmp_enable_pin; // TIM2_CH4
#else
typedef quan::mcu::pin<quan::stm32::gpioa,2>    usart2_txo_rxi_pin;// USART2_TX
typedef quan::mcu::pin<quan::stm32::gpioa,3>    video_spi_clock;// TIM9_CH2
#endif

typedef quan::mcu::pin<quan::stm32::gpioa,4>    fsk_dac_out_pin; // NOT MOVABLE

#if !defined(QUAN_AERFLITE_BOARD)
typedef quan::mcu::pin<quan::stm32::gpioa,5>    dac2_out_pin; // NOT MOVABLE
#else
typedef quan::mcu::pin<quan::stm32::gpioa,5>    video_in_tim2_hsync_pin; // CSYNC TIM2_CH1
#endif

#if !(defined QUAN_DISCOVERY)
#if !defined(QUAN_AERFLITE_BOARD)
typedef quan::mcu::pin<quan::stm32::gpioa,6>    av_dac_nsync; // software no af
typedef quan::mcu::pin<quan::stm32::gpioa,7>    av_dac_data; // softawre no af
#else
typedef quan::mcu::pin<quan::stm32::gpioa,6>    video_in_tim3_hsync_pin ;  // TIM3_CH1 csync and internal out 
typedef quan::mcu::pin<quan::stm32::gpioa,7>    ppmsum_in_pin; // TIM14_CH1
#endif
#endif

#if defined(QUAN_AERFLITE_BOARD)
typedef quan::mcu::pin<quan::stm32::gpioa,8>    i2c3_scl ;
#endif
#if defined(QUAN_AERFLITE_BOARD)
typedef quan::mcu::pin<quan::stm32::gpioa,9>    usart1_txo_pin; // USART1_TX
typedef quan::mcu::pin<quan::stm32::gpioa,10>   usart1_rxi_pin; // USART1_RX
#else
typedef quan::mcu::pin<quan::stm32::gpioa,9>    mavlink_txo_pin; // USART1_TX
typedef quan::mcu::pin<quan::stm32::gpioa,10>   mavlink_rxi_pin; // USART1_RX
#endif
#if defined(QUAN_AERFLITE_BOARD)
typedef quan::mcu::pin<quan::stm32::gpioa,11>   can1_rx;
typedef quan::mcu::pin<quan::stm32::gpioa,12>   can1_tx;
#endif

typedef quan::mcu::pin<quan::stm32::gpioa,13>   swdio;
typedef quan::mcu::pin<quan::stm32::gpioa,14>   swdclk;
#if defined(QUAN_AERFLITE_BOARD)
// The JTAG debug pins are also LED outputs, but connected to mosfet gates so
// can be overridden by JTAG functionality
typedef quan::mcu::pin<quan::stm32::gpioa,13>   notify_led1;
typedef quan::mcu::pin<quan::stm32::gpioa,14>   notify_led2;
#endif

#if !defined(QUAN_AERFLITE_BOARD)
typedef quan::mcu::pin<quan::stm32::gpioa,15>   video_in_tim2_hsync_pin ; // TIM2_CH1 ( also TIM2_ETR)
#else
typedef quan::mcu::pin<quan::stm32::gpioa,15>   imu_nss_pin; // SPI1_NSS hardware nss pin
#endif
//----PORTB---------------------------------------------
#if !defined(QUAN_AERFLITE_BOARD)
typedef quan::mcu::pin<quan::stm32::gpiob,0>    video_adc_pin ; // ADC12_IN8
typedef quan::mcu::pin<quan::stm32::gpiob,1>    vin_voltage_pin ;//adc1 ADC12_IN9 
typedef quan::mcu::pin<quan::stm32::gpiob,2>    boot1_pin;
#else
typedef quan::mcu::pin<quan::stm32::gpiob,0>    rcout5_pin; // TIM1_CH2N
typedef quan::mcu::pin<quan::stm32::gpiob,1>    rcout6_pin;  // TIM1_CH3N
typedef quan::mcu::pin<quan::stm32::gpiob,2>    video_isync_pin;// BOOT0 high for internal video
#endif

#if defined(QUAN_AERFLITE_BOARD)
typedef quan::mcu::pin<quan::stm32::gpiob,3>    spi1_sck; // imu
typedef quan::mcu::pin<quan::stm32::gpiob,4>    spi1_miso; // imu
typedef quan::mcu::pin<quan::stm32::gpiob,5>    spi1_mosi; // imu

typedef quan::mcu::pin<quan::stm32::gpiob,6>    rcout1_pin; 
typedef quan::mcu::pin<quan::stm32::gpiob,7>    rcout2_pin; 
typedef quan::mcu::pin<quan::stm32::gpiob,8>    rcout3_pin; 
typedef quan::mcu::pin<quan::stm32::gpiob,9>    rcout4_pin; 
#endif

#if defined(QUAN_AERFLITE_BOARD)
typedef quan::mcu::pin<quan::stm32::gpiob,10>   usart3_txo_pin; // USART3_TX
typedef quan::mcu::pin<quan::stm32::gpiob,11>   usart3_rxi_pin; // USART3_RX
#else
typedef quan::mcu::pin<quan::stm32::gpiob,10>   frsky_txo_pin; // USART3_TX
typedef quan::mcu::pin<quan::stm32::gpiob,11>   frsky_rxi_pin; // USART3_RX
#endif
#if !(defined QUAN_DISCOVERY)
typedef quan::mcu::pin<quan::stm32::gpiob,12>   heartbeat_led_pin;
#endif

typedef quan::mcu::pin<quan::stm32::gpiob,13>   video_mux_out_black_sck; // SPI2_SCK AF5 input from pixelclk
#if !defined(QUAN_AERFLITE_BOARD)
typedef quan::mcu::pin<quan::stm32::gpiob,14>   video_in_hsync_first_edge_pin; // TIM12_CH1
#else
typedef quan::mcu::pin<quan::stm32::gpiob,14>   video_mux_out_black_miso; // actually MASK 
#endif
typedef quan::mcu::pin<quan::stm32::gpiob,15>   video_in_hsync_second_edge_pin; // TIM12_CH2
//-----PORTC---------------------------------------
#if defined(QUAN_AERFLITE_BOARD)
typedef quan::mcu::pin<quan::stm32::gpioc,0>    video_adc_pin; //ADC123_IN10
typedef quan::mcu::pin<quan::stm32::gpioc,1>    analog_in; //ADC123_IN11 undedicated anlog input
#endif
#if !defined(QUAN_AERFLITE_BOARD)
typedef quan::mcu::pin<quan::stm32::gpioc,2>    video_mux_out_black_miso; // SPI2_MISO AF5
#else
typedef quan::mcu::pin<quan::stm32::gpioc,2>    analog_rssi_in; 
typedef quan::mcu::pin<quan::stm32::gpioc,3>    analog_batt_current_in; //ADC123_IN13
typedef quan::mcu::pin<quan::stm32::gpioc,4>    analog_batt_voltage_in; //ADC123_IN14
typedef quan::mcu::pin<quan::stm32::gpioc,5>    analog_airspeed_in; //ADC123_IN15
#endif
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

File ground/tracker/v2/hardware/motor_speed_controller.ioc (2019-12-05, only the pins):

Mcu.UserName=STM32L432KCUx
PA0.Signal=OPAMP1_VINP
PA1.Signal=COMP1_INP
PA10.Signal=GPXTI10
PA11.Signal=GPXTI11
PA12.Signal=GPXTI12
PA2.GPIO_Label=VCP_TX
PA2.Signal=USART2_TX
PA3.Signal=OPAMP1_VOUT
PA4.Signal=ADCx_IN9
PA5.Signal=SPI1_SCK
PA6.Signal=S_TIM16_CH1
PA8.Signal=S_TIM1_CH1
PA9.Signal=S_TIM1_CH2
PB0.Signal=SPI1_NSS
PB1.Signal=ADCx_IN16
PB5.Signal=SPI1_MOSI
PB6.Signal=I2C1_SCL
PB7.Signal=I2C1_SDA

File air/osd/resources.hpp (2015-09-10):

#ifndef QUANTRACKER_AIR_OSD_RESOURCES_HPP_INCLUDED
#define QUANTRACKER_AIR_OSD_RESOURCES_HPP_INCLUDED

/*
 Copyright (c) 2013 -2015 Andy Little 

 With Grateful Acknowledgements to the prior work of:
   Sami Korhonen(Openpilot.org)
   taulabs ( taulabs.com) 
   brainFPV ( brainfpv.com)
   Thomas Oldbury (super-osd.com)

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
 You should have received a copy of the GNU General Public License
 along with this program. If not, see <http://www.gnu.org/licenses/>
*/

#include <quan/stm32/freertos/freertos_usart_task.hpp>
#include <quan/voltage.hpp>
#include <quan/stm32/gpio.hpp>
#include <quan/stm32/spi.hpp>
#include <quan/stm32/tim.hpp>
#include <quan/stm32/usart.hpp>

#if (QUAN_OSD_BOARD_TYPE == 4)
#include "processor/board_type4.hpp"
#else
//timers
typedef quan::stm32::tim1                       spi_clock_timer;
typedef quan::stm32::tim2                       video_columns_gate_timer;
typedef quan::stm32::tim3                       video_rows_line_counter;
typedef quan::stm32::tim6                       fsk_dac_timer;
#if defined QUAN_OSD_SOFTWARE_SYNCSEP
/*
   2 channel timer us channels 1 and 2 for getting sync pulse length
   and length of a line etc
*/
typedef quan::stm32::tim9                       sync_sep_timer;
#endif
/*
   To avoid use of SPI loading the video color dac is done
   with an interrupt of the timer
*/
typedef quan::stm32::tim10                      video_level_dac_irq_timer;
/*
 Not used currently for transmitter,but wil be eventually
 to transmit the telem at start of video frame
*/
typedef quan::stm32::usart1                     av_telemetry_usart;
typedef quan::stm32::usart2                     frsky_usart; // maybe inverted but not on f4
typedef quan::stm32::usart3                     posdata_usart;
// usart4 avail for expansion
// usart6 avail for expansion
//spi
// SPI1 avail for expansion
typedef quan::stm32::spi2                       video_mux_out_black_spi;
typedef quan::stm32::spi3                       video_mux_out_white_spi;
// I2C1 and I2C3 avail for expansion
//----PORTA---------------------------------------
#if !defined QUAN_DISCOVERY
typedef quan::mcu::pin<quan::stm32::gpioa,0>    usart4_tx ;
#endif
#if defined QUAN_OSD_TELEM_RECEIVER
typedef quan::mcu::pin<quan::stm32::gpioa,1>    telem_cmp_enable_pin; // TIM2_CH2
#else 
//USART4_TX
typedef quan::mcu::pin<quan::stm32::gpioa,1>    usart4_rx; 
#endif

#if !(defined QUAN_OSD_SOFTWARE_SYNCSEP)
#error need to sort pins here

 typedef quan::mcu::pin<quan::stm32::gpioa,2>    video_in_odd_even_pin ; // no special requirements!
#else
// POSS move pixel clock here on TIM9
// move frsky_txo_pin to PC12 uart 5
typedef quan::mcu::pin<quan::stm32::gpioa,2>    frsky_txo_pin;  // USART2 TX or TIM5 CH3
#endif
//##############################
//pa3 free frsky rx
// only for compile .. need to do tx only usart for freertos
// TIM5_CH4 
typedef quan::mcu::pin<quan::stm32::gpioa,3>    frsky_rxi_pin_unused;  // not used ... 
// 
//#########################
typedef quan::mcu::pin<quan::stm32::gpioa,4>    fsk_dac_out_pin; // also also SPI1_NSS
// prob most useful to do audio..
typedef quan::mcu::pin<quan::stm32::gpioa,5>    dac2_out_pin;
/*
PA6 TIM13_CH1 SPI1_MISO
PA7 TIM14_CH1 SPI1_MOSI
*/
#if defined QUAN_DISCOVERY
typedef quan::mcu::pin<quan::stm32::gpioa,8>  video_spi_clock ; // TIM1_CH1
#else
typedef quan::mcu::pin<quan::stm32::gpioa,8>  i2c3_scl ;
#endif
#if !(defined QUAN_DISCOVERY)
typedef quan::mcu::pin<quan::stm32::gpioa,9>    heartbeat_led_pin;
#endif
typedef quan::mcu::pin<quan::stm32::gpioa,10>   frsky_txo_sign_pin;
/*
CAN protocol useful?
PA11 - CAN1 TX
PA12 - CAN1 RX
*/
/*
SWD
PA13    SWDIO
PA14    SWCLK
*/
typedef quan::mcu::pin<quan::stm32::gpioa,15>   video_in_tim2_hsync_pin ; // TIM2_CH1 ( also TIM2_ETR) also SPI1_NSS
//----PORTB---------------------------------------------
/*
PB0  TIM8_CH2
PB1  TIM8_CH3
*/
#define TEST_OUTPUT_PIN_ENABLE 1
typedef quan::mcu::pin<quan::stm32::gpiob,2>    test_output_pin;

#if defined QUAN_DISCOVERY
typedef quan::mcu::pin<quan::stm32::gpiob,3>    video_mux_out_white_sck; // SPI3_SCK AF6
typedef quan::mcu::pin<quan::stm32::gpiob,4>    video_mux_out_white_miso; // SPI3_MISO AF6
#else
// SPI port for expansion
typedef quan::mcu::pin<quan::stm32::gpiob,3> spi1_sck;
typedef quan::mcu::pin<quan::stm32::gpiob,4> spi1_miso;
typedef quan::mcu::pin<quan::stm32::gpiob,5> spi1_mosi;
#endif
#if defined QUAN_OSD_TELEM_TRANSMITTER
typedef quan::mcu::pin<quan::stm32::gpiob,6>    av_video_txo; // USART1 TX
#endif
#if defined QUAN_OSD_TELEM_RECEIVER
typedef quan::mcu::pin<quan::stm32::gpiob,7>    av_video_rxi; // USART1_RX  fast 10.5 Mbps
#else
// I2C port for expansion
typedef quan::mcu::pin<quan::stm32::gpiob,7>    i2c1_sda; 
typedef quan::mcu::pin<quan::stm32::gpiob,8>    i2c1_scl;
#endif
/*
PB9 TIM11_CH1 TIM4_CH4 I2C1_SDA
*/
#if !defined QUAN_DISCOVERY
// also bootloader via usart
typedef quan::mcu::pin<quan::stm32::gpiob,10>     posdata_txo_pin; // SF:USART3_TX:AF7
typedef quan::mcu::pin<quan::stm32::gpiob,11>     posdata_rxi_pin; // SF:USART3_RX:AF7
#endif
/*
PB12 - general purpose - no useful SF
*/
typedef quan::mcu::pin<quan::stm32::gpiob,13>   video_mux_out_black_sck; // SPI2_SCK AF5
typedef quan::mcu::pin<quan::stm32::gpiob,14>   video_mux_out_black_miso; // SPI2_MISO AF5
/*
PB15 TIM8 CH3 TIM12 CH2
*/
//-----PORTC---------------------------------------
/*
PC0 ADC
PC1 ADC
PC2 ADC
PC3 ADC
PC4 ADC
PC5 ADC
*/
#if !(defined QUAN_OSD_SOFTWARE_SYNCSEP)
typedef quan::mcu::pin<quan::stm32::gpioc,6> video_in_vsync_pin ; // TIM3_CH1
#else
typedef quan::mcu::pin<quan::stm32::gpioc,6> usart6_tx;
typedef quan::mcu::pin<quan::stm32::gpioc,7> usart6_rx;
#endif
/*
PC8 TIM8_CH3 
*/
#if ! defined QUAN_DISCOVERY
typedef quan::mcu::pin<quan::stm32::gpioc,9> i2c3_sda ;
#endif

#if !defined QUAN_DISCOVERY
typedef quan::mcu::pin<quan::stm32::gpioc,10>     video_mux_out_white_sck; // SPI3_SCK 
typedef quan::mcu::pin<quan::stm32::gpioc,11>     video_mux_out_white_miso; // SPI3_MISO
#endif
/*
// could move frsky tx here and get another usart
PC12  UART5_TX
PC13  GP no af
*/
// NA on 64 pin part except PD2 PH0 PH1
//---------PORTD--------------------------------
/*
PD0 GP no useful AF
*/
typedef quan::mcu::pin<quan::stm32::gpiod,1>     av_dac_nsync; // software no af
typedef quan::mcu::pin<quan::stm32::gpiod,2>     video_in_tim3_hsync_pin; // TIM3_ETR
typedef quan::mcu::pin<quan::stm32::gpiod,3>     av_dac_data; // software no af
/*
PD4
PD5
PD6
*/
typedef quan::mcu::pin<quan::stm32::gpiod,7>     av_dac_clk; // software no af
#if defined QUAN_DISCOVERY
typedef quan::mcu::pin<quan::stm32::gpiod,8>     posdata_txo_pin; // SF:USART3_TX:AF7
typedef quan::mcu::pin<quan::stm32::gpiod,9>     posdata_rxi_pin; // SF:USART3_RX:AF7
#endif
typedef posdata_txo_pin debug_txo_pin ;
typedef posdata_rxi_pin debug_rxi_pin;

#if (defined QUAN_DISCOVERY) && (defined QUAN_STM32F4)

typedef quan::mcu::pin<quan::stm32::gpiod,12>   green_led_pin;   // green led on Discovery
typedef quan::mcu::pin<quan::stm32::gpiod,13>   orange_led_pin;       // orange led on Discovery
typedef quan::mcu::pin<quan::stm32::gpiod,14>   heartbeat_led_pin;
typedef quan::mcu::pin<quan::stm32::gpiod,15>   blue_led_pin;       // blue led on Discovery
#else
typedef quan::mcu::pin<quan::stm32::gpiod,12>   tim4_ch1;   
typedef quan::mcu::pin<quan::stm32::gpiod,13>   tim4_ch2;     
typedef quan::mcu::pin<quan::stm32::gpiod,14>   tim4_ch3;
typedef quan::mcu::pin<quan::stm32::gpiod,15>   tim4_ch4;    
#endif
//----------PORTE--------------------------
/*
PE0
PE1
PE2
PE3
PE4
*/
#if defined QUAN_OSD_SOFTWARE_SYNCSEP
// need move to other timer on 64 pin
typedef quan::mcu::pin<quan::stm32::gpioe,5> video_in_hsync_first_edge_pin; // TIM9_CH1
typedef quan::mcu::pin<quan::stm32::gpioe,6> video_in_hsync_second_edge_pin; // TIM9_CH2
#endif
/*
PE7
PE8
*/
#if ! defined QUAN_DISCOVERY
//could move to other timer on APB2 bus
typedef quan::mcu::pin<quan::stm32::gpioe,9> video_spi_clock; // TIM1_CH1
#endif
/*
PE10
PE11
PE12
PE13
PE14
PE15
*/
//----------------PORTH---------------

#if (QUAN_OSD_BOARD_TYPE == 2 )  || (QUAN_OSD_BOARD_TYPE == 3 )
void Dac_setup();
// for 8 bit only msbyte of val is used
// code is 00 write to specific reg but dont update
// 1 is write to specific reg and update outputs
// 2 is write tao all registers and update outputs
// 3 is power down outputs
// really only 0 1nd 1 are useful
void Dac_write(uint8_t ch, quan::voltage::V const & vout, uint8_t code);

#endif

typedef quan::stm32::freertos::usart_tx_rx_task<
   posdata_usart,
   2,20, 
   posdata_txo_pin,posdata_rxi_pin,
   uint8_t
> posdata_tx_rx_task;

typedef quan::stm32::freertos::usart_tx_rx_task<
   frsky_usart,
   10,2, 
   frsky_txo_pin,frsky_rxi_pin_unused,
   char
> frsky_tx_rx_task;
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

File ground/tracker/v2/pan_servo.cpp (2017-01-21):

#include <stm32f4xx.h>
#include <FreeRTOS.h>
#include <task.h>

#include <quan/max.hpp>
#include <quan/stm32/sys_freq.hpp>
#include <quan/angle.hpp>
#include <quan/reciprocal_time.hpp>
#include <quan/frequency.hpp>
#include <quan/voltage.hpp>
#include <quan/current.hpp>
#include <quan/time.hpp>
#include <quan/meta/integer_max.hpp>
#include <quan/stm32/get_raw_timer_frequency.hpp>
#include <quan/stm32/push_pop_fp.hpp>
#include "resources/tracker_resources.hpp"
#include "resources/osd_resources.hpp"
#include "tracker_commands.hpp"
/*
   pan servo
   With current test rig
   Clockwise rotation of the spindle gives a positive back emf
   setting Dir = 1 gives positive rotation
   Interrupts are chained
   Since they are low priority, ensure that there is a minimum delay
   (say 20 us) so that interrupts always serviced
    Need to sort a  way to recover if interrupts missed .. watchdog?

    Change so that Uif is set to period longer than max of pwm period
    Use compare to do chained interrupts and use uif to reset to start if
    no compare before overflow. Uif should provide a warning if tripped
*/

/*
   Should be possible to do better
   At start of cycle
      1)setup for a current ADC conversion triggered by timer set to the on duty cycle and enable EOC irq.

      2) in the EOC irq, turn off the motor and calc the time to start emf sampling
      setup for emf ADC conversions in a dma sequence.
      setup the trigger time to the first conversion but setup timer dma to fire once to
      modify the period (TIMx_ARR) once first conv is underway to the period for repeated emf ADC conversion
      and setup the ADC DMA to the number of conversions

      3) In emf conversions DMA complete irq, calc pwm etc and restart the cycle

     ADC can be triggered by various timer channels  of TIM1, TIM2,TIM3, TIM4, TIM5, TIM8
      see ref_man section 10.6 table 35  
*/

namespace {

   // Potentially useful output units
   // assuming we want to track in radians per sec
   // rad is the value_type.. should be be used like e.g float
   // pedantic use of units here. could use e.g float but got radians type so may as well use it!
   typedef quan::angle::rad rad;
   typedef quan::reciprocal_time_<rad>::per_s rad_per_s;

   // this value updated by the external tracker logic
   // The servo is servoing on this value
   rad_per_s target_output_angular_velocity{rad{0.f}};

   // the angular velocity we want the tracker pan output to be at 
   // nominal 1/50th sec pan_motor_pwm_period
   constexpr quan::time::us pan_motor_pwm_period{20000.f};

   // using LD39015 3.3V reg voltage output accuracy quoted as +- 2%
   // 
   constexpr quan::voltage::mV volts_per_bit = quan::voltage::mV{3300.f}/4096.f;

 // ################ flash variables ############
   // default to 1 rev per sec with 12v input
   // needs to be measured for a particular setup
   auto constexpr output_angular_velocity_per_mV 
   = rad_per_s{quan::angle::two_pi} 
         / quan::voltage::mV{12000};

   // proportional constant tried with kP =0.3 and kD = 0.6 on small motor
   // works ok
   auto  kP = 0.1f/rad_per_s{rad{1.f}};
   // differential constant is always 2 x proportional
   auto  kD = 0.2f/rad_per_s{rad{1.f}};
   // 0.1 gives a minimum on pulse of 2 ms 
   // needs to be big enough to move the motor rateher
   // than just causing buzzing
   float min_duty_cycle = 0.05f;
   // constant for current dependent delay
   // after switching off motor
   // set here to a spike of 2 ms per 1 A current
   auto constexpr current_spike_constant = quan::time::us{2000.f}/quan::current::mA{1000.f};

   //####### end flash variables ###############

   // where the zero volts rail is should be approx half of supply
   // actual value found at  startup by reading the 
   // motor with no input until it is in some range
   // e.g so not being moved by user
   quan::voltage::mV emf_zero_volts_rail{1650.f};
   // If using  ACS712 current sensor also need a  zero volts rail
   // value found at startup
   quan::voltage::mV current_zero_volts_rail{1650.f};

   // duty cycle as fraction of period somewhere between -1 and 1
   // (accumulated)
   float duty_cycle = 0.f;
   // std::abs(duty_cycle) max limit
   // need some velocity samples!
    float max_duty_cycle = 0.75f;

   // velocity error from prev iter
   rad_per_s old_velocity_error{rad{0.f}};

   bool pan_motor_enabled = false;

   // keeps a tally of how much of cycle used by each section
   quan::time::us cycle_time_left = pan_motor_pwm_period;
   void section_start_new_cycle();
   // set initial interrupt
   void (*pf_timer_irq_section_function)() = &section_start_new_cycle;
   
   void set_next_timer_irq(quan::time::us t, void(*pfn)())
   {
     pf_timer_irq_section_function = pfn;
     int32_t time_to_irq = static_cast<int32_t>(t.numeric_value());
     if ( time_to_irq < 0){
         time_to_irq = 10;
     }
     pan_motor_timer::get()->arr = time_to_irq;
     cycle_time_left -= t;
     pan_motor_timer::get()->cnt = 0U;
     quan::stm32::enable<pan_motor_timer>();
   }
  
   void section_switch_on_motor();
   void section_start_backemf_sampling();

   // accumulator for velocity( back_emf) sampling
   quan::voltage::mV back_emf_sum{0};
   // used to record number of velocity samples this cycle
   uint32_t num_backemf_samples = 0U;

   // recalced each cycles
   quan::voltage::mV motor_back_emf{0};
   quan::current::mA motor_current{0};
   // the pid loop on velocity
  // int led_counter = 0;
   void section_start_new_cycle()
   {
//      ++led_counter;
//      if (led_counter == 50){
//         led_counter = 0;
//        // quan::stm32::complement<heartbeat_led_pin>();
//      }
      // reinvigorate for new cycle
      cycle_time_left = pan_motor_pwm_period;
      // get motor angular velocity by averaging samples from last cycle
      // but avoid divison by zero
      motor_back_emf =
      ( num_backemf_samples > 0)
         ? (back_emf_sum / num_backemf_samples) - emf_zero_volts_rail
         : quan::voltage::mV{0};
      // constrain to a min
      if (quan::abs(motor_back_emf) < quan::voltage::mV{5}){
         motor_back_emf = quan::voltage::mV{0};
      }
      rad_per_s const actual_output_velocity = motor_back_emf * output_angular_velocity_per_mV;
      // get term proportional to velocity error
      rad_per_s const velocity_error = target_output_angular_velocity - actual_output_velocity;
      duty_cycle += kP * velocity_error;
      // get term proportional to rate of change of velocity error
      rad_per_s const velocity_error_de_dt = velocity_error - old_velocity_error;
      old_velocity_error = velocity_error;
      duty_cycle += kD * velocity_error_de_dt;
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

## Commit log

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2013-05-23 made rotation centre same as physical centre so it should be slightly easier to build.
    [tracker_v1.fcstd]
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2013-05-25 got most bits on. Just need to sort hole between batbox and rest
    [tracker_v1.fcstd]
2013-05-25 looks pretty goo now. Just need sort slot in part between two bits
    [tracker_v1.fcstd]
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2013-06-01 added cutout for video connectors etc and redid cut in battery box front
    [tracker_v1.fcstd]
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2013-12-10 more work on pcb- made smaller and changed zenner for a mosfte transistor,passes tests in Kicad. Must check pinout of mosfet though
    [air1.brd, air1.sch]
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2014-02-10 revert led.cpp so not using foreach std::ref etc.. Tested running and init error led flashing again
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2014-03-03 changed optimisation from Os to O3 and moved clearing of exti to just after it was read as set. Now seems to be not giving exti failed messages. So looks like its stable at the mo
    [f4_discovery.sch]
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2014-04-04 refit xtal on board as was in as 1206 but in fact is bigger
    [air1.brd]
2014-06-06 changed previously incorrect (On quantracker air V1.0) pinouts of LM1117 voltage reg and MCP601R op amp, but not redone connections yet
    [air1.brd, air1.sch, test1.scad]
2014-07-01 add default to case to prevent warning about returning unknown value in switch
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2014-07-12 streamlining air pcb for v2, remove eeprom and lp filter components and added buffers etc
    [air1.sch]
2014-08-04 incorporated digital fsk demod routine, got flashhing lights, indicating getting data, now to test if tracking.EDIT: Tested in garden, and seems to track ok so fp context appears to be saving correct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
    [air1.sch, f4_discovery.sch, modem_rx.sch]
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2014-08-08 Now uses 2 ADC channels and subtracts difference giving a great reduction in noise
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2014-10-28 moved in original osd code to air/osd. No other work on it
    [bcv61_sync_clamp.sch, costs.ods, mcu.sch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]
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2014-11-12 trying to get video osd part working, but failing in this version, not using all rtos stuff, now to try just osd
    [heartbeat_task.cpp, main.cpp]
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2014-11-13 removed testing writes to orange and heartbeat leds. Tested by connecting to APM on Skaredykat and go heartbeat led flashing correctly. Good
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2014-11-25 osd cleared up hierearchy and changed expansion to use 64 pin DIP 0.9 with 2 x psus on, which can be linked if not reqd
    [camera.sch, expansion.sch, hub.sch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]
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2014-11-30 osd tidying and added reset to header connector
    [$savepcb.brd, camera.sch, expansion.sch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]
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2014-12-02 added resistors to output port on board and satrted on boardtype 4 port but currently in transition
    [$savepcb.brd, camera.sch, expansion.sch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]
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2014-12-03 on pcb added battery level resistor divider. On code compiled and built ok but not uploaded or tested
    [camera.sch, expansion.sch, mavlink_port.sch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]
2014-12-04 fix typos in osd dac.cpp and modify makefile for boardtype 4 dicovery version
2014-12-04 uncommented makefile options for board type 3 after several mods, compiled, built uploaded and running ok for board_type3. Compiled and built with board_type4 and board_type4 disco but not uploaded a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
    [versions.ods]
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2014-12-05 uploaded and tested boardtype 4. Some text appears on screen but not right at all
    [versions.ods]
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2014-12-07 must be nearly finalised pcb ready for sending off.Disco circuit tested so now just hope its right for pcb
    [camera.sch, expansion.sch, mavlink_port.sch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]
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2014-12-12 getting conversions between encoder and compass bearing aligned and add config file which needs to be loaded after each firmware upload
    [tracker_config_file.txt]
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2015-02-05 knacked stash will revert
    [main.cpp, resources.hpp]
2015-02-05 shorten invoke for uploading with stm32flash
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2015-03-04 removed traces on pcb design. Added links to separate ground paths for modules. Moved mpu to other side of board. Added 2 pin power conector at end of board
    [camera.sch, expansion.sch, mavlink_port.sch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]
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2015-03-07 semi wired, now to try making more traces on one side orthogonal to other
    [osd_64_lite.brd]
2015-03-07 moving pins around on expansion, but reckon I will get routing donr
    [camera.sch, expansion.sch, mavlink_port.sch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]
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2015-03-08 nearly all joined up now. Just to do plenty of neat and tidying
    [camera.sch, expansion.sch, mavlink_port.sch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]
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2015-03-08 osd v2 pcb drc check reports no errors, now to flesh out trace widths etc
    [osd_64_lite.brd]
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2015-03-10 now looking pretty good. Need todo text and redo copper pour areas
    [osd_64_lite.brd]
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2015-03-19 working flash example but problem with initing flash in mavlink task, prob need to sort serial output for dbugging, e.g start sp init flash then stop sp or something
    [main.cpp]
2015-03-20 use lightweight sp for flash, to avoid ram use and rtos use
    [board_type4.hpp, main.cpp]
2015-03-25 fix flash_menu bug(mostly in quan-trunk, added utility to write vars from a file
    [osd_params.txt]
2015-04-02 corrected some wrong pin labels on text layer
    [osd_64_lite.brd]
2015-04-03 first commit of refactored OSD with more stuff brought out to user
    [telem_timing.ods]
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2015-04-13 added flash param to optionally invert frsky_tele sp tx pin
    [osd_params.txt]
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2015-04-29 moved scad files out from V2 to clear way for V2 tracker code
    [ballra.g, ballrace_blank.stl, circlip.stl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]
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2015-05-28 velocity pan servo working though sometimes sticks for some reason, maybe after invalid text comand input
    [osd_v2_1_board.sch, pan_motor.sch, tracker_using_quantracker_osd.sch]
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2015-06-08 issue with pan motor
    [slewing_ring.fcstd]
2015-06-09 added sockets. now need to widen upper case slightly for pan motor to fit
    [3_5mm_jack_socket.fcstd, slewing_ring.fcstd]
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2015-06-10 sort better method of holding up mag gps shelf with a 6mm carbon tube slider. Add balance connector. Add sides of upper cover.Next to work out how to attach tilt servo
    [16mm_gear_motor.fcstd, gear_motor_mount.fcstd, slewing_ring.fcstd]
2015-06-10 final offsets of antenna_mount pockets I hope. swapped power and video connectors for better clearance from tilt servo. Added tilt servo mount but needs cutting
    [servo_mount.fcstd, slewing_ring.fcstd]
2015-06-10 move uper base up to correct position and create upper case basic extrusion
    [slewing_ring.fcstd]
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2015-06-11 got some sort of UpperCase with some fillets and shell, so hope can live with it
    [slewing_ring.fcstd]
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2015-06-12 update servo mount so it can be fitted into position. Not finished yet
    [servo_mount.fcstd]
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2015-06-15 completed main bulk of new tracker hardware. Just some details to do. Modified compass arrow bitmaps for osd_example1 etc
    [db9.fcstd, lcd.fcstd, rca_socket.fcstd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]
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2015-06-16 switched osd air v2.1 diode to front for more space. Now prior to adding some beads
    [osd_64_lite.brd]
2015-06-17 added some 3 terminal EMI filters to the board
    [camera.sch, expansion.sch, mavlink_port.sch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]
2015-06-17 finalising v2.2 board. Added some emi filters and ground planes on top and bottom layers
    [osd_64_lite.brd]
2015-06-17 added pullups so video will be pass through at startup I hope\!
    [camera.sch, expansion.sch, mavlink_port.sch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]
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2015-06-18 replace inductor cap LP filters with induuctor only filters since other filter place constarints on input voltage. Now added some component info incluidnf fotprint , precise part number and lonk to d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
    [camera.sch, expansion.sch, mavlink_port.sch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]
2015-06-18 made a separate version of the air osd pcb project for clarity
    [camera.sch, expansion.sch, mavlink_port.sch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]
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2015-06-25 changed diode pins side to comply with IPC-7351 2005 (dont have later spec)
    [camera.sch, expansion.sch, mavlink_port.sch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]
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2015-07-02 various cleanups of the source, but will need to rebui,d all apps. Will be a few problems
    [main.cpp]
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2015-07-06 moved pin setup to libs, cleaned up osd_example1 makefie to use osd,osd.hpp, added some docs
    [magnetometer.sch, osd_v2_1_board.sch, pan_motor.sch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]
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2015-07-07 osd not working in this commit
    [main.cpp]
2015-07-08 pretty broken, no mag exti and some debug text but actually providing compass output to OSD display
    [main.cpp, pan_servo.cpp, resources.hpp]
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2015-07-28 adjusted the timing of tim3 (hsync) to subtract 1 from timing coinstants and seesm to have removed jitter now
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2015-08-31 modified sync sep code tested and working. Occasionally looks like some horz lines are missed, so maybe adjust hsync filter yet, but overall looks stable
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2015-10-30 only filter noise if its a receiver for PlayUAVOSD
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2015-11-27 just update version info of the kicad flight controller schematic and lib, but no real chanes there
    [flight_controller.sch]
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2016-01-12 add errors count to vid frame rx telemetry example
2016-01-12 minor rework of tracker v2 hardware
    [slewing_ring.fcstd]
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2016-04-12 fix typo in analog switch name
    [video_circuit.sch]
2016-04-12 fix up kicad local libraries
    [camera.sch, expansion.sch, mavlink_port.sch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]
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2016-10-01 due to short circuit and swap_buffers was not being called so do swap_buffers first
2016-10-01 use lines not text for now since looks like font colours arent correct
    [main.cpp]
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2017-01-20 update i2c error messages to get build working
2017-01-20 replace critical with susuepend resume. temporarly remove i2c error diagnostic
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2017-05-11 in testing, starting up without video connnected get green led but mechanics seem to hang, but if video is connected then disconnected on plane , then just maodem telem seesm to work ok. Need to redo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
    [main.cpp]
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

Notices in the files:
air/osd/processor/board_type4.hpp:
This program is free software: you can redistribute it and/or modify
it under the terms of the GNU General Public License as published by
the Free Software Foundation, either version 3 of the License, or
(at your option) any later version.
